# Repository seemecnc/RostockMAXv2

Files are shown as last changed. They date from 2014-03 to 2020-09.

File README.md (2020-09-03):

# Rostock MAX v2 3D Printer by SeeMeCNC #

### A hybrid design between the Rostock MAX build volume and Orion delta shape and overall design. ###

### Larger build volume than Orion Delta (similar to Rostock MAX) but much faster assembly and stiffer frame###

#### Build volume is appx. 11" diameter by 14+" tall. ####

# Visit seemecnc.com for documentation under the menu tab SUPPORT > ARCHIVE

Specs:

Overall machine size - 20" diameter by 40" tall (including spool mounted on top)

Power Supply - 450w ATX PSU (12v 20+amps)

Heated Bed - Onyx (same as Rostock MAX)

Electronics - RAMBo by UltiMachine

Filament - 1.75mm ABS/PLA/HIPS/Taulman Nylon/T-Glase/other 
Anything withe less than 240c printing temps

HotEnd - SeeMeCNC 1.75mm bowden 

Extruder - EZStruder set up as bowden drive

Human/Machine interface - LCD control with onboard SD card

Frame material - HP Melamine laminate

These files are distributed openly without warranty, as is/where is under the GPL liscense from previous inspirational designs such as the Rostock by Johann. The EZ Struder was inspired by whosawhatsis as well as sgraber's i3 extruders.

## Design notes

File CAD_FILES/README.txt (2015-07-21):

For Injection Molded/CNC Machined part source files, see the RostockMAX github repo.
The parts are same for V1 / v2

7/21 J.O.
REV5 dxf files eliminated the lasercut truck plates for cheapskates since moving to I.M. style and opened up some clearance holes for thumb screws to mount the side covers and LCD panel

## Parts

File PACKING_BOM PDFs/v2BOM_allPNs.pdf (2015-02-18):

# Packing List

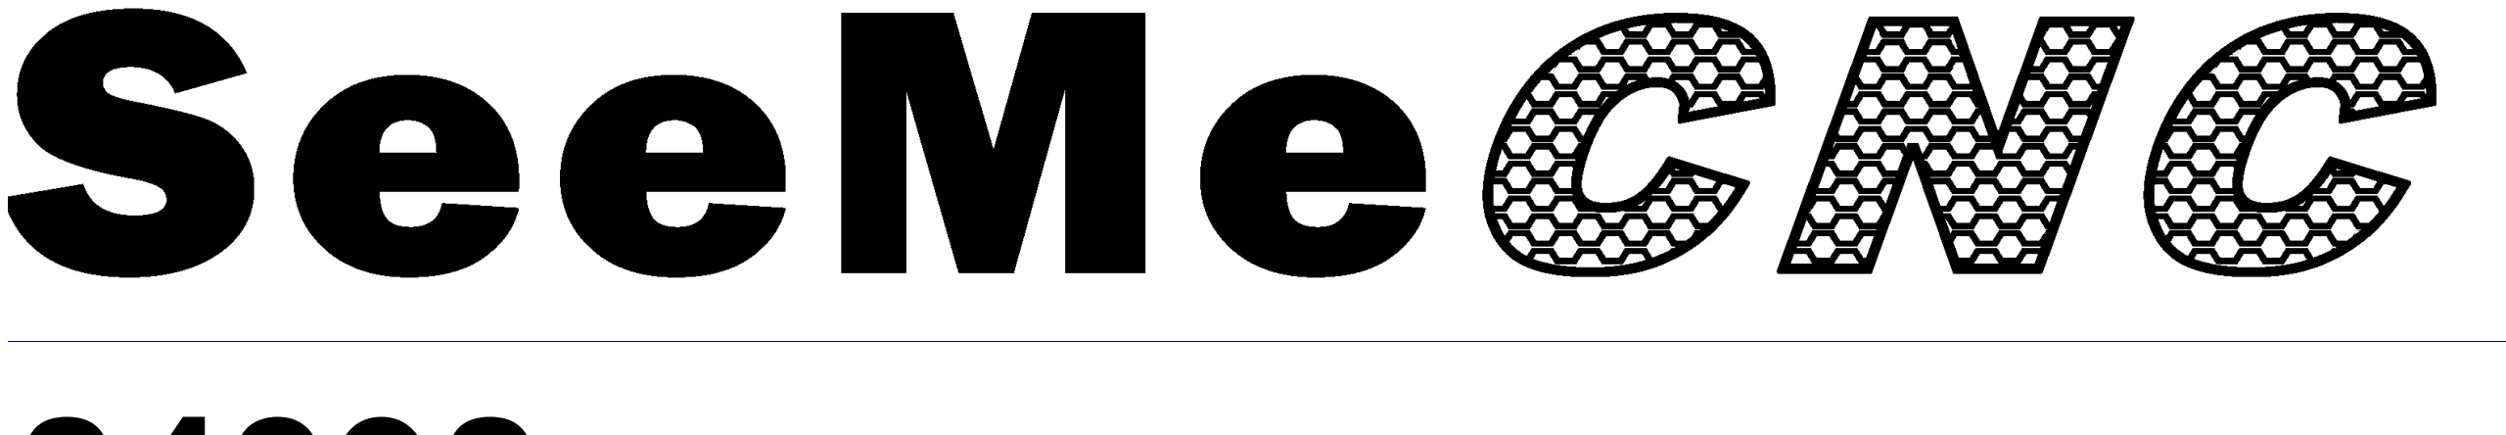
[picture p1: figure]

# 84398 Rostock MAX V2 3D Printer Kit BLACK

item # | qty | Description | Where is this item used?
84301 | 1 | Laser Cut Sheets (3 full 1 partial)
84302 | 1 | Smoke Acrylic Parts Pack
84392 | 1 | Rostock MAX V2 Electronics Parts and Hardware Pack 4 (inside box)
26702 | 1 | ATX Power Supply 450W
26602 | 1 | Borosilicate Glass Build Plate 300mm Dia. X 3mm Thick ( inside box)
84395 | 1 | Rostock MAX V2 Hardware Pack 3 (inside box)
84391 | 1 | Rostock MAX V2 Hardware Pack 1 (inside box)
84393 | 1 | Rostock MAX V2 Hardware Pack 2 (inside box)
68310 | 3 | T Slot Rail 1" (25mm) Square x 32" (812mm) Long Aluminum
©2014 SeeMeCNC | 18-Feb-15 | 84398 | Rostock MAX V2 3D Printer Kit BLACK | Page 1 of 1

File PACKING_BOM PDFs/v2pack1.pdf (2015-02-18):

# Packing List

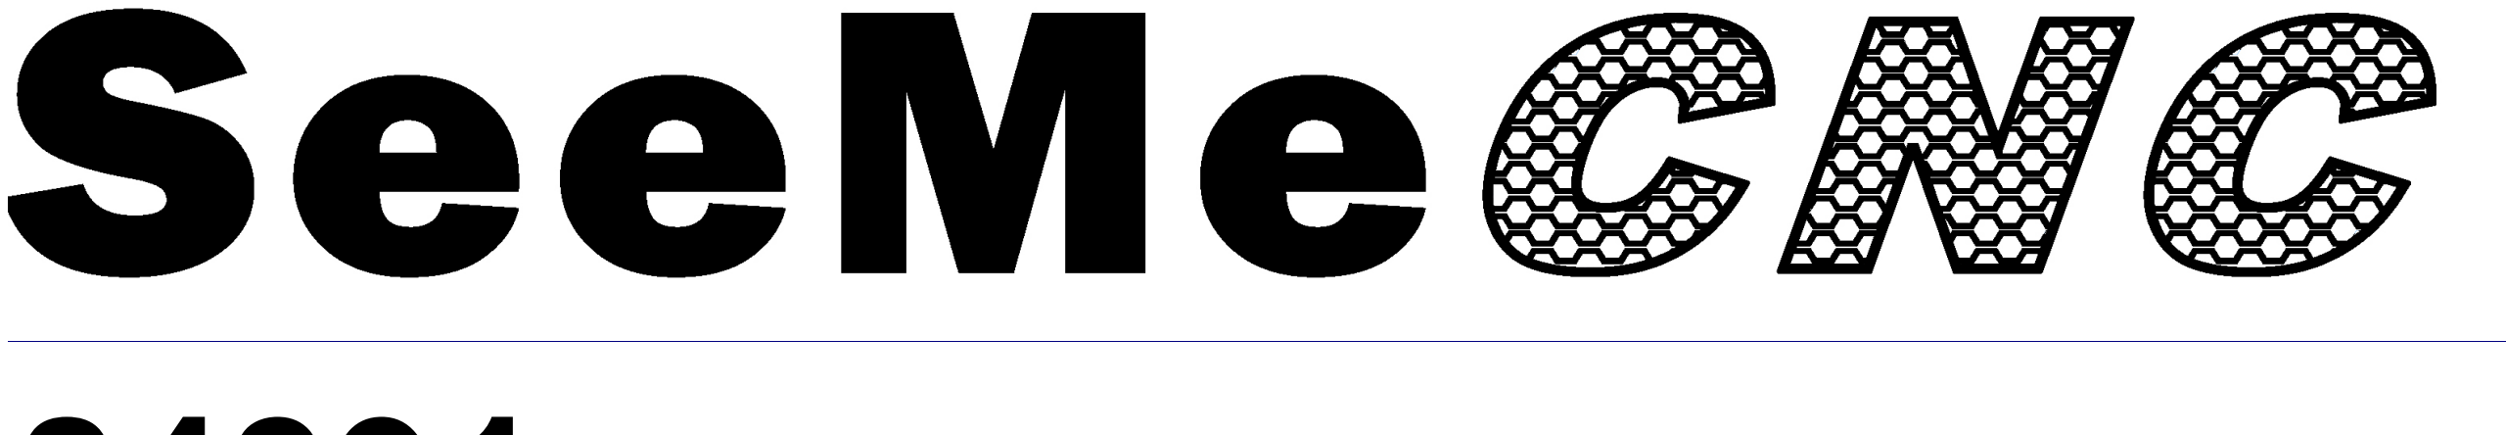
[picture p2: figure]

# 84391 Rostock MAX V2 Hardware Pack 1

item # | qty | Description | Where is this item used?
44010 | 6 | Rubber Foot | | On the bottom of the baseplate.
17505 | 6 | Leg for 44010 Foot | | On the bottom of the baseplate.
30450 | 18 | #6 SAE Flat Washer Stainless Steel | ONLY used on the 608 idlers that go in the top/bottom of the tslot rails.
30449 | 6 | #4 SAE Flat Washer Stainless Steel | Belt clamp screws.
35065 | 21 | 608 Ball Bearing | | Cheapskates and belt idlers.
30650 | 14 | 2-56 x 5/8"L Pan Head Phillips Machine Screw ( zinc plate ) | 4 for the LCD faceplate and 6 for mounting endstops.
30222 | 10 | 4-40 Blind T-Nut (zinc plate) | belt clamping and RAMBo mounting
29999 | 1 | SHCS 10-32 x 5/8 L 18-8 SS | To tap holes for 10-32 nylon thumb screws.
29998 | 6 | 10-32 x 5/8" Pan Head Screw Nylon | On the bottom of the baseplate.
30170 | 6 | 10-32 Nylon Finish Nut | On the bottom of the baseplate.
30172 | 9 | 10-32 x 3/4" Knurled Thumb Screw Black Nylon | Right/left base covers and holds LCD panel on.
30121 | 4 | 6-32 x 1/2" Slotted Pan Head Screw Nylon | PSU mounting.
30033 | 31 | 6-32 x 1" L Phillip Pan Head Screw Stainless | Misc. general assembly of base/table and extruder mount/spoolholder.
30006 | 6 | SHCS 6-32 x 5/8" | 18-8 SS | For mounting the U Joint mounts to the cheapskate plates.
30034 | 12 | 6-32 x 1.75" L Phillip Pan Head Screw Stainless | 608 idlers in motor mounts and tops and also 3 for the hotend standoffs
30164 | 63 | 6-32 Nylon Lock Nut Stainless Steel | All 6-32 hardware gets these lock nuts.
30037 | 14 | 6-32 x 2.0" L Phillip Pan Head Screw 18-8 SS | Cheapskate plates that hold bearings and 2 for the EZStruder mounting.
30135 | 15 | 6-32 x 1/2" 18-8 SS Phillips Flat Head | Inside of base and top side plates, to retain acrylic panels, and 3 endstop trig
30419 | 25 | 1/4-20 x 1/2" Button Head Cap Screw Stainless | T slot mounting.
32005 | 25 | T SLOT Nut for 1" size 1/4-20 | T slot mounting
30236 | 4 | 4-40 x 3/4"L Phillip Flat Head Machine Screw Stainless | For mounting RAMBo to electroncis mount.
30232 | 6 | 4-40 x 1/2" L SHCS Stainless | Belt clamps.
30642 | 14 | 2-56 Finish Nuts ( zine plate ) | 4 for the LCD faceplate and 6 for mounting endstops.
30250 | 14 | #4 Pan Head Phillips x 3/8" Sheet Metal Type B - Stainless Steel | 2 for LCD sides, rest for t slot stop screws inside motor mount plates to keep
30318 | 12 | M3 - .50 x1 0mm Phillip Pan Head Machine Screw 18-8 SS | Stepper motor mounting.
©2014 SeeMeCNC | 18-Feb-15 | 84391 | Rostock MAX V2 Hardware Pack 1 | Page 1 of 1

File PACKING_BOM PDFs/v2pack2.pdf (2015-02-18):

# Packing List

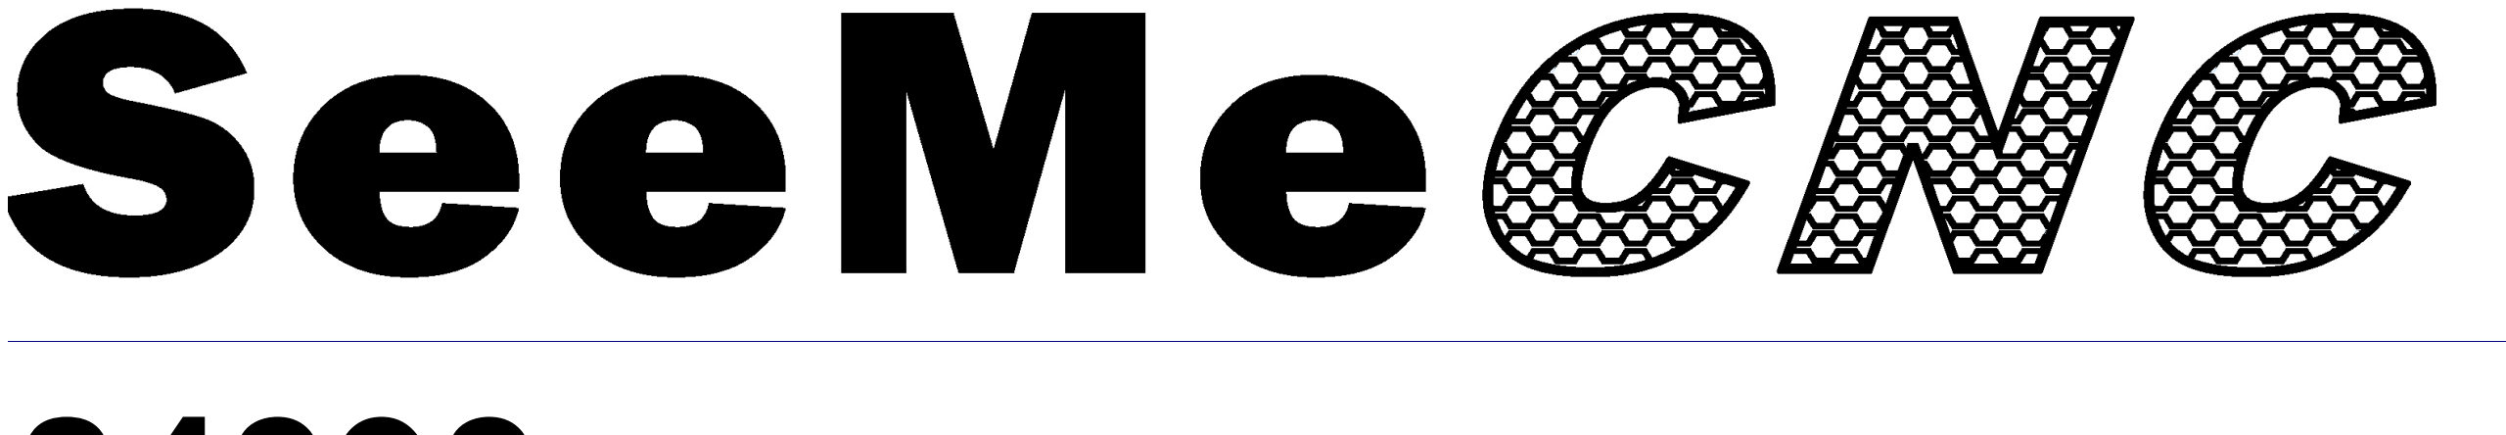
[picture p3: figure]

# 84393 Rostock MAX V2 Hardware Pack 2

item # | qty | Description | Where is this item used?
68326 | 12 | 608 Cheapskate Carriage Bearing Spacer | Fixed black spacers for cheapskates.
68340 | 18 | 608 Cheapskate Idler Bearing Spacer | Large black round spacers for belt idlers.
68315 | 12 | 608 Cheapskate Eccentric Carriage Tensioner Spacer | Eccentric grey cammed parts for adjusting tension.
68334 | 3 | Hot End Platform Spacer (machined Aluminum) | 1" long.
68325 | 6 | Universal Joint Axle 3-1/8" Long
68309 | 12 | Universal Joint (Machined Aluminum)
©2014 SeeMeCNC | 18-Feb-15 | 84393 | Rostock MAX V2 Hardware Pack 2 | Page 1 of 1

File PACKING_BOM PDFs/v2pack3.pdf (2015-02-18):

# Packing List

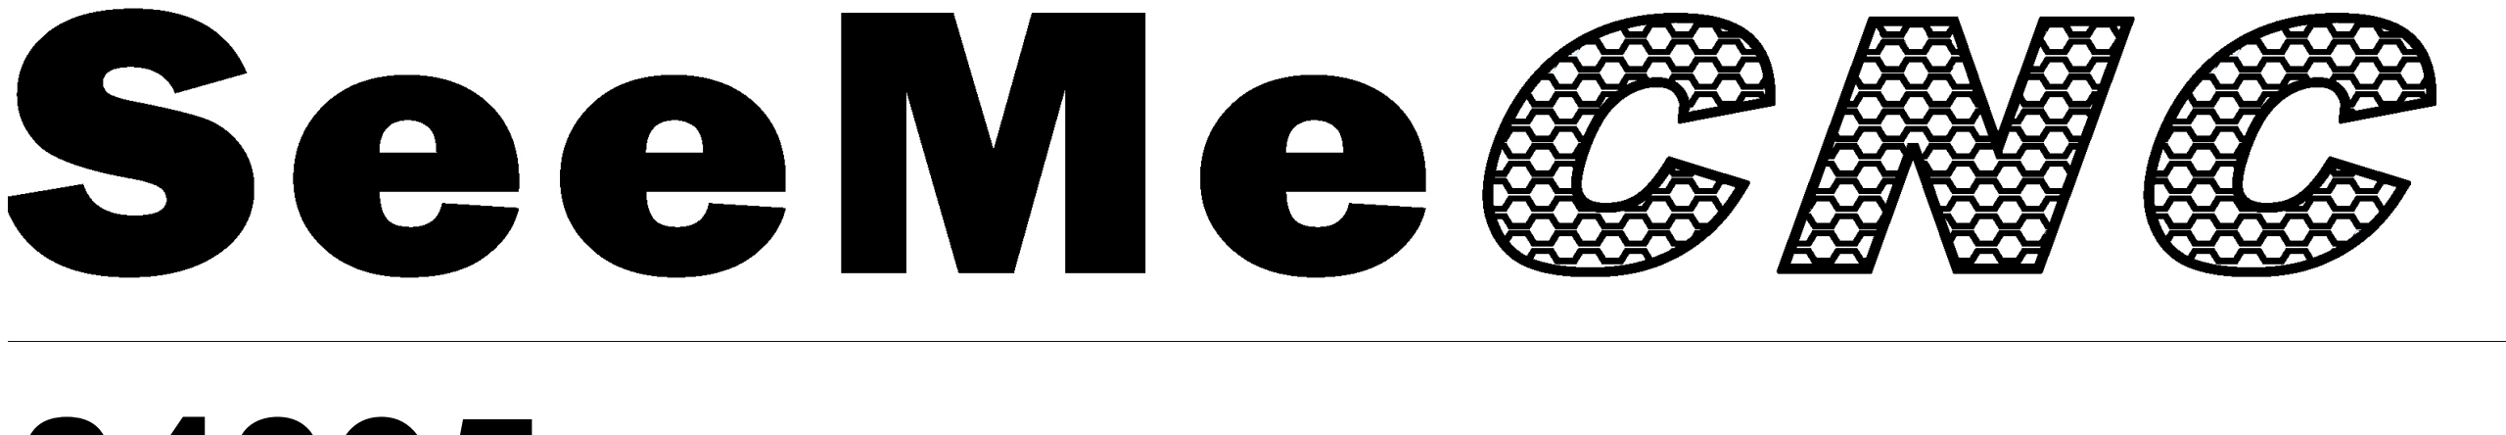
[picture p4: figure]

# 84395 Rostock MAX V2 Hardware Pack 3

item # | qty | Description | Where is this item used?
71505 | 20 | Plastic Bearing Roller 1/8"ID x 3/8"OD x 0.156"W | 4 for RAMBo mount and 6 for belt clamps.
26164 | 12 | Wire Tie (small) | To make neater wiring, esp. for strain relief on hotend platform and to attach
39835 | 1 | 20T Timing Pulley GT2 2mm Pitch (Pack of 3 w/6 setscrews and allen key)
68332 | 3 | Carriage Base for Universal Joint (injection molded) | Outer 'tabs' have been removed to allow spring clips to be used.
70832 | 1 | Platform (Spring Clip Style)
87940 | 6 | Spring Clip for U Joint
71566 | 1 | Gear (15 Tooth) | To press on stepper shaft for hand turning the extruder.
58761 | 6 | Binder Clip | For clamping glass build plate.
©2014 SeeMeCNC | 18-Feb-15 | 84395 | Rostock MAX V2 Hardware Pack 3 | Page 1 of 1

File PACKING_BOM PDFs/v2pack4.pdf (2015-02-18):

# Packing List

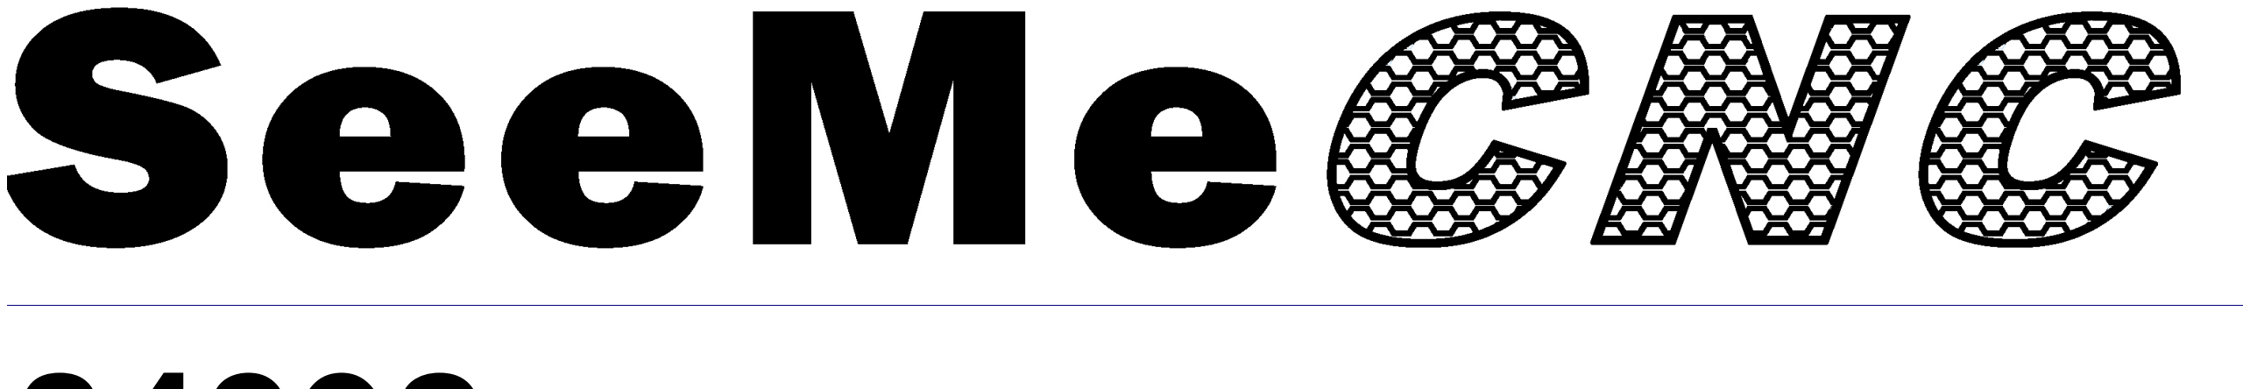
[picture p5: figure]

# 84392 Rostock MAX V2 Electronics and Hardware Pack 4

item # | qty | Description | Where is this item used?
26710 | 1 | RAMBo Electronic Control Board
26708 | 1 | USB Cable
58770 | 1 | Onyx Heated Bed Kit | Includes 6 4-40 x 3/4" flat heads, 6 4-40 t nuts, 6 plastic bearing roller, thermi
26720 | 1 | LCD Smart Controller With SD Card
26711 | 1 | LCD to RAMBo Adapter Kit
26169 | 1 | Knob Soft Touch 5mm ID | For LCD.
26501 | 4 | Nema 17 Stepper Motor 4800gcm holding torque | For three towers and extruder motor.
26175 | 1 | Rocker Switch, Black Round | Power switch.
26174 | 2 | Spade Terminal Crimp for Switch | For use on new power switch to make it removeable.
26309 | 1 | Fan 25mm X 25mm X 10mm | PEEK blower fan.
26173 | 1 | FAN 40mm x 40mm x 10mm | RAMBo cooling fan, goes on back of RAMBo electroncis mount blowing ON t
26722 | 10 | 22/4 Wire (by the foot) | For extending stepper motor for extruder.
26728 | 15 | 26AWG 7 Strand Wire BLACK Thin Wall PVC (by the foot) | For hotend PEEK fan and PART fan.
26726 | 15 | 26AWG 7 Strand Wire RED Thin Wall PVC (by the foot) | For hotend PEEK fan and PART fan.
26727 | 4 | 3/8" Dia. Expandable Black Mesh Loom (by the foot) | For wiring going from top plate down to platform.
26729 | 3 | 5/16" Heat Shrink Tubing (by the inch) | For cleaning up the ends of the mesh loom.
39910 | 1 | Timing Belt GT2 series 2mm pitch Neoprene (3 pieces 76" long)
68336 | 24 | Bearing Sleeve | For cheapskates.
68303 | 6 | ARM for Rostock MAX
70780 | 1 | EZStruder Cold End Kit | Includes stepper motor mounting hardware.
68394 | 1 | 1.75mm Bowden Hot End Assembly | Includes all hotned parts to assemble hotend, and 24" bowden tube w/ 2 ptc fi
26171 | 1 | Blower 30mm X 30mm X 10mm 12V DC | 0
26172 | 2 | Butt Splice Connector 16-14AWG | Hot End
26721 | 10 | 18/4 Wire (by the foot) | Hot End / Thermistor Wiring
©2014 SeeMeCNC | 18-Feb-15 | 84392 | Rostock MAX V2 Electronics and Hardware Pack 4 | Page 1 of 1

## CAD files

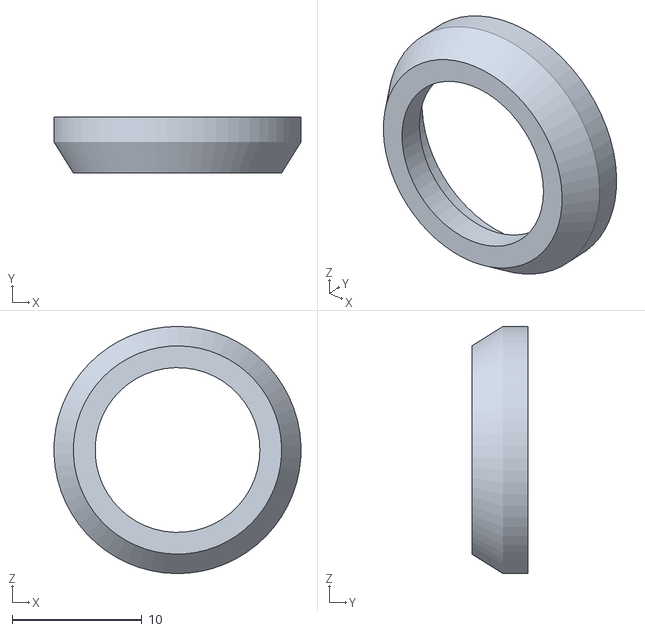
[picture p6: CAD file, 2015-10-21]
CAD_FILES/STL/843XX Rostock Max v2 Assembly - 70850 IM Ball Joint Carriage Assembly AXLE-4 87941 Bearing Sleeve-1.STL
19.0 x 4.35 x 19.0

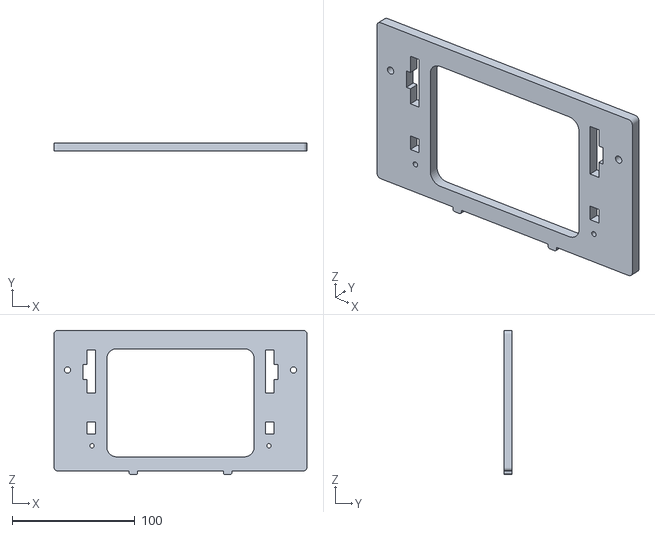
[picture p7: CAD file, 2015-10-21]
CAD_FILES/STL/843XX Rostock Max v2 Assembly - 87912 LCD Frame-1.STL
206.0 x 6.90 x 117.5

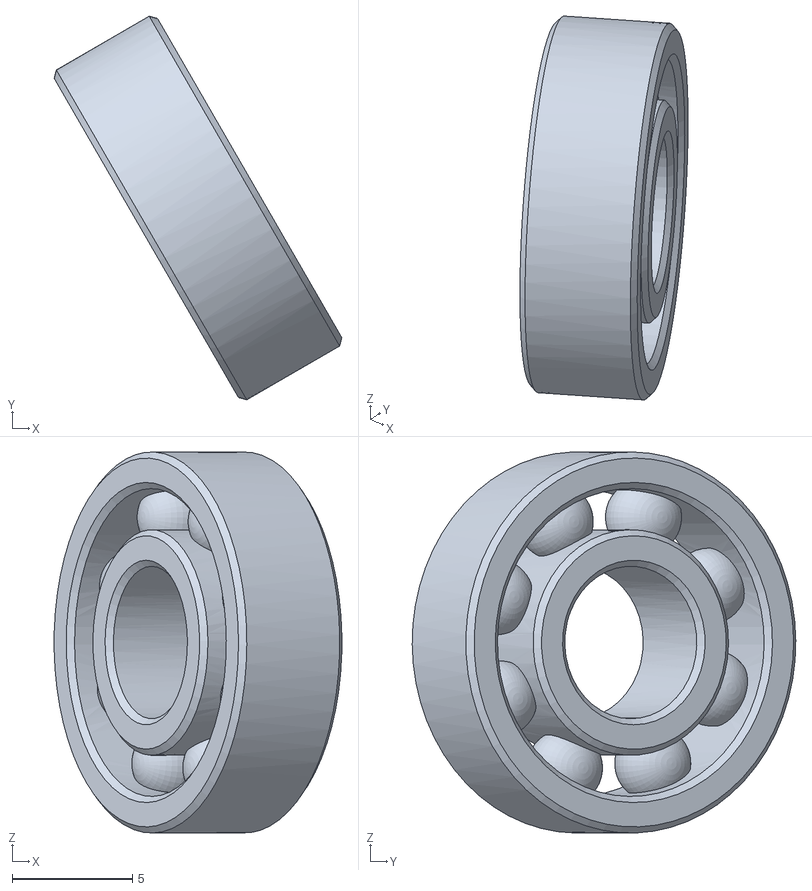
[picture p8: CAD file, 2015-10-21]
CAD_FILES/STL/843XX Rostock Max v2 Assembly - 70850 IM Ball Joint Carriage Assembly AXLE-5 0250ID - 0625OD - 0196W-1.STL
12.0 x 16.0 x 15.9

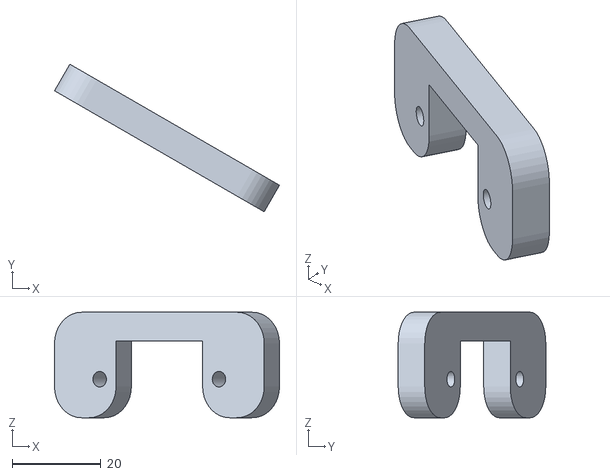
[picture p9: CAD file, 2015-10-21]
CAD_FILES/STL/843XX Rostock Max v2 Assembly - 70769 Spacer-3.STL
50.6 x 33.2 x 23.8

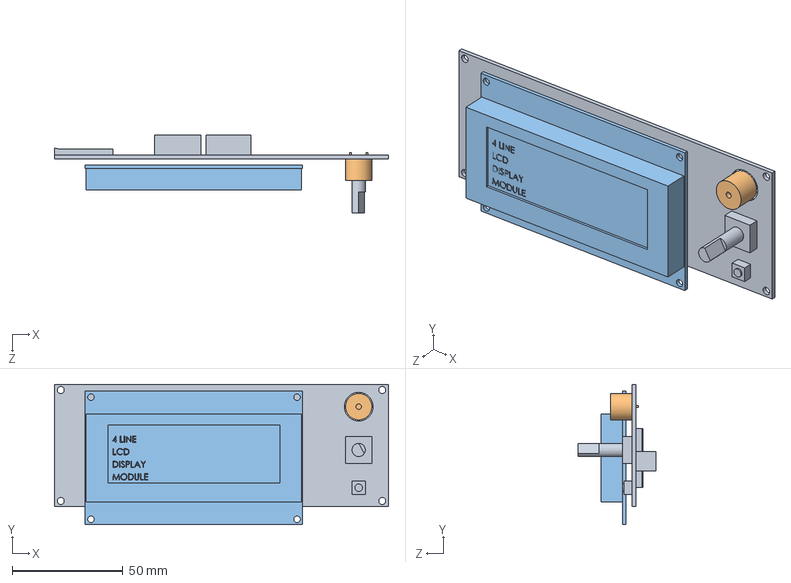
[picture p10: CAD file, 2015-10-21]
CAD_FILES/Solidworks/Smart Controller reprapdiscount.SLDASM
150.5 x 63.2 x 35.0 mm
MAIN_BOARD_reprapdiscount_smart_controller
Piezo Beeper HSD
LCD 4 Line reprapdiscount style

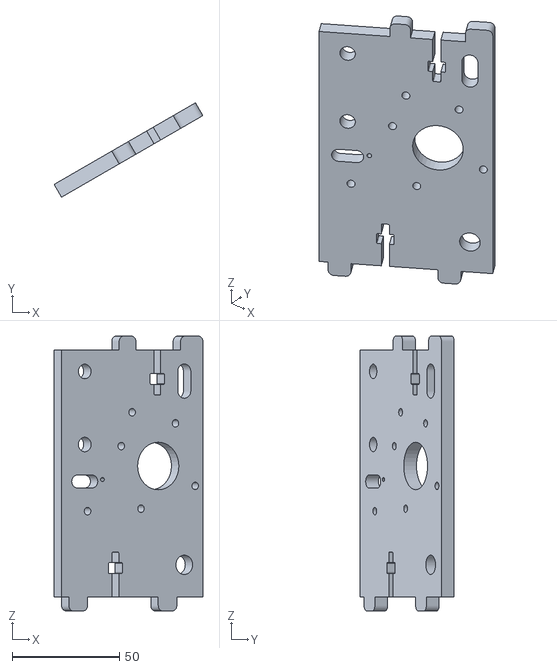
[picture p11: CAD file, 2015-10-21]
CAD_FILES/STL/843XX Rostock Max v2 Assembly - XZ Stepper Motor Assembly-1 84307Motor Mount-1.STL
69.3 x 44.0 x 128.0

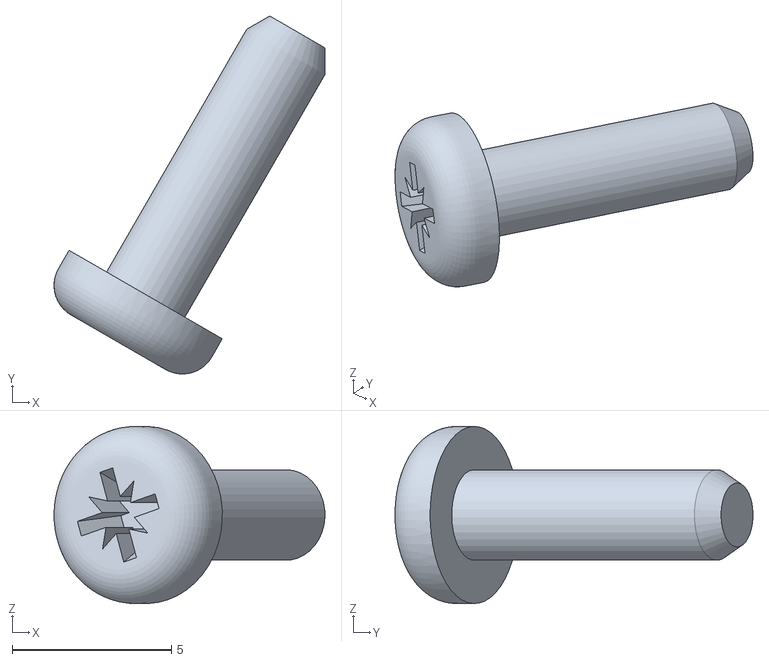
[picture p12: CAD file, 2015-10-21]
CAD_FILES/STL/843XX Rostock Max v2 Assembly - 70780 EZStruder-1 No 4 x 0375L PANHTS SS Sheet Metal PANHTS 0.112-24-type II-B-0.375-N-5.STL
8.51 x 11.2 x 5.56

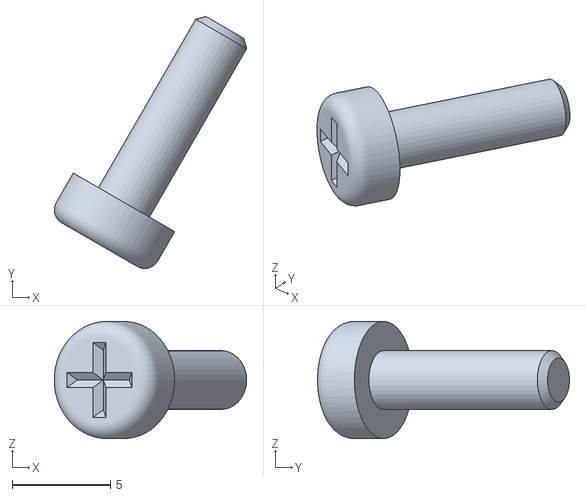
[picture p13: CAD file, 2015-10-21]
CAD_FILES/STL/843XX Rostock Max v2 Assembly - Y Stepper Motor Assembly-1 M3-0.5 x 10mm L Phillip Pan Head Stainless-4.STL
9.80 x 12.8 x 5.97

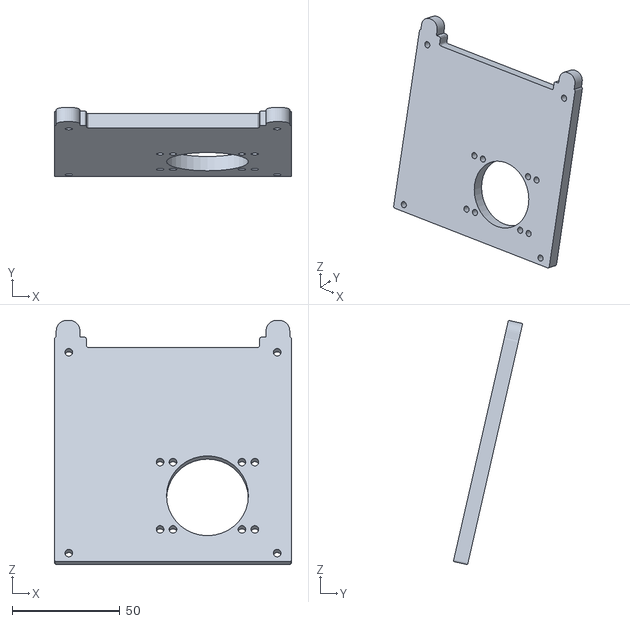
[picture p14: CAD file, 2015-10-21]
CAD_FILES/STL/843XX Rostock Max v2 Assembly - 84328 Rambo Mounting Plate-1.STL
110.0 x 32.2 x 113.5

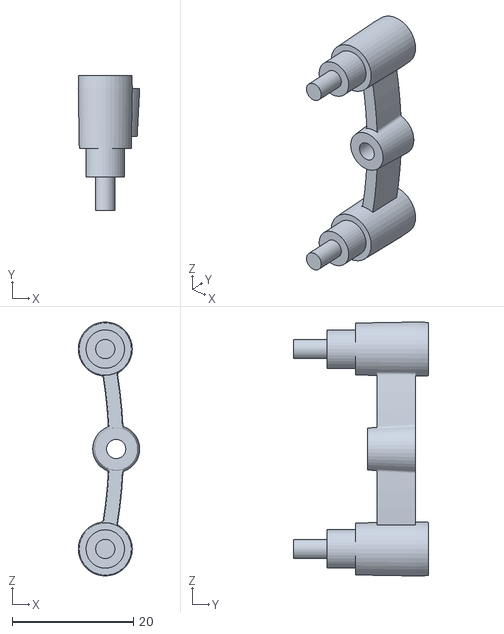
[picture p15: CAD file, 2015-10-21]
CAD_FILES/STL/843XX Rostock Max v2 Assembly - 70850 IM Ball Joint Carriage Assembly AXLE-4 70853 Outer Carriage Spring Arm-1.STL
10.2 x 22.2 x 41.9

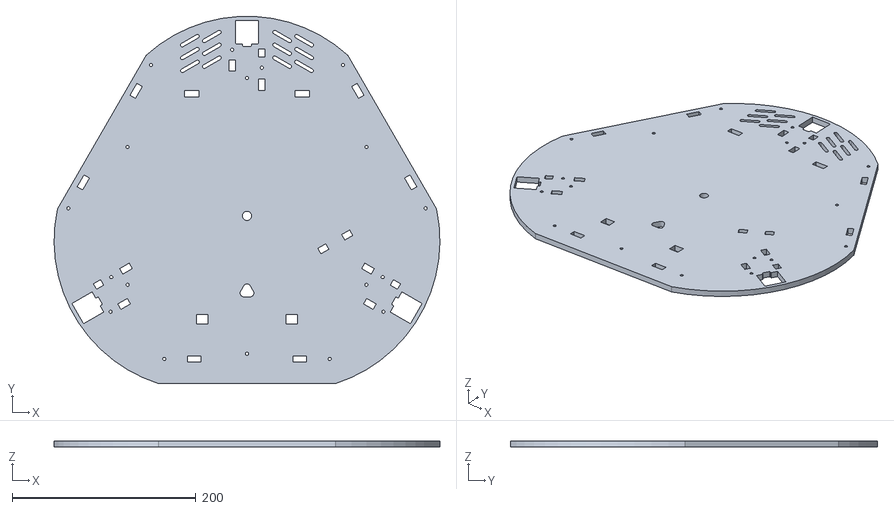
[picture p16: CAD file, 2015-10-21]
CAD_FILES/STL/843XX Rostock Max v2 Assembly - 84303 Base Top-Plate-1.STL
419.9 x 399.3 x 6.80

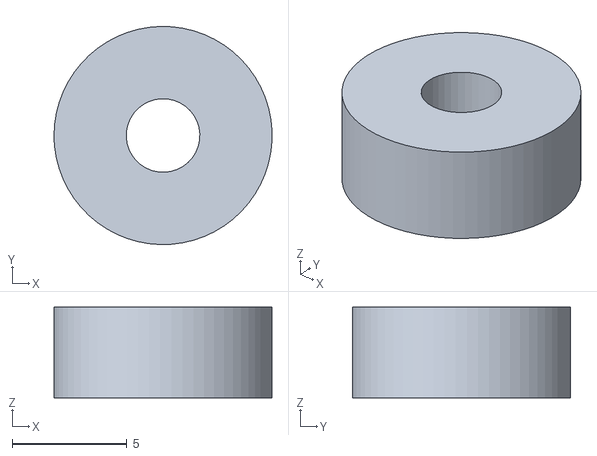
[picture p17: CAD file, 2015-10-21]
CAD_FILES/STL/843XX Rostock Max v2 Assembly - 71505 Plastic Bearing 0125ID x 0375OD x 0156W-7.STL
9.52 x 9.52 x 3.97

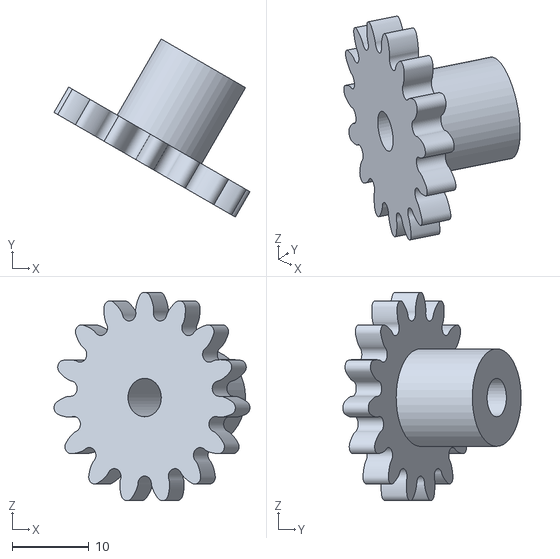
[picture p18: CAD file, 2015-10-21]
CAD_FILES/STL/843XX Rostock Max v2 Assembly - 70780 EZStruder-1 71566 Gear 15T 0950PD-1.STL
25.5 x 23.2 x 27.1

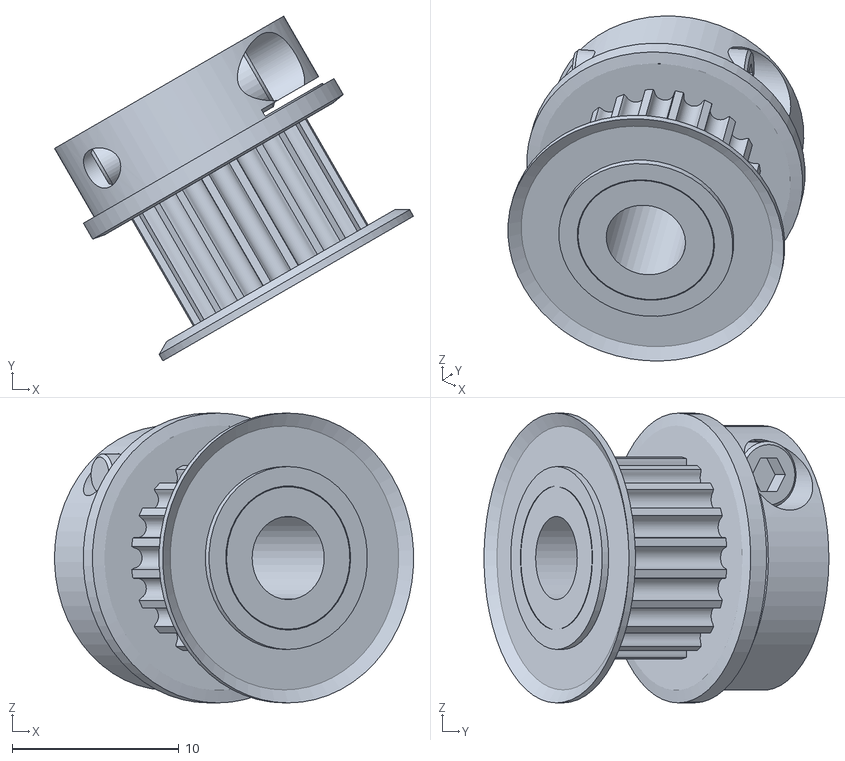
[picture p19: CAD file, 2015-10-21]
CAD_FILES/STL/843XX Rostock Max v2 Assembly - XZ Stepper Motor Assembly-1 39835 Timing Pulley 20T GT2-2-1.STL
21.6 x 20.7 x 17.4

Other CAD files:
CAD_FILES/IGES/843XX Rostock Max v2 Assembly.IGS
CAD_FILES/STL/843XX Rostock Max v2 Assembly - 84305 Side-3.STL
CAD_FILES/STL/843XX Rostock Max v2 Assembly - XZ Stepper Motor Assembly-2 39835 Timing Pulley 20T GT2-2-1.STL
CAD_FILES/STL/843XX Rostock Max v2 Assembly - 70850 IM Ball Joint Carriage Assembly AXLE-7 No 4 x 0250L PANHTS SS Sheet Metal PANHTS 0.112-24-type II-B-0.25-N - Copy-3.STL
CAD_FILES/IGES/0250ID - 0625OD - 0196W.IGS
CAD_FILES/IGES/17505 LEG.IGS
CAD_FILES/IGES/39835 Timing Pulley 20T GT2-2.IGS
CAD_FILES/IGES/4-40 X 0500 PHILLIP FLAT HEAD.IGS
CAD_FILES/IGES/44010 FOOT.IGS
CAD_FILES/IGES/58763 Bed Insulator for Onyx R5.IGS
CAD_FILES/IGES/6-32 X 0500 Phillip Flat Head Screw Stainless.IGS
CAD_FILES/IGES/6-32 X 1 PHILLIP FLAT HEAD.IGS
CAD_FILES/IGES/608-bearing.IGS
CAD_FILES/IGES/68325 U Shaft Axle.IGS
CAD_FILES/IGES/68340 Bushing Washer 3mm.IGS
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

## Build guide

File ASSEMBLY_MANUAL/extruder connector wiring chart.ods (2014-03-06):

Pin | Color
1 | Green
2 | Red
3 | Black
4 | White

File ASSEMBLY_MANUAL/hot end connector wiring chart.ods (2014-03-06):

Pin | Color
1 | Red
2 | Black
3 | Green
4 | White

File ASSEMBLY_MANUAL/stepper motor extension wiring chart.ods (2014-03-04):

Pin | Stepper Color | Extension Color
1 | Green | Green
2 | Red | Red
3 | Blue | Black
4 | Yellow | White

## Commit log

2014-02-04 Initial Upload
    Uploading merged CAD files from MCX of Rostock/Orion and laying out R3
    files
2014-02-04 Updated mcx file
    updated colors for laser
2014-02-04 more cad updates
2014-02-04 added logo
    added logo, fixed hole orientation
2014-02-05 cad updates
    updating top plate mounting
2014-02-06 Laying out Top cover plate
    Layed out cover for top and acrylic parts
2014-02-06 added new top plate and onyx ins
    added insulator and relyaed some parts
2014-02-06 more cad updates
    more updates
2014-02-06 added DXF of MCX file
    Added DXF file THIS MAY NOT BE CURRENT FILES DUE TO NOT EXPORTING THE
    DXF FROM MCX ! ! !
    [LC_270-SHEETS.DXF]
2014-02-06 updated cad
2014-02-06 cad fixes
    need to move side plates on right/left back some more
2014-02-07 updated cad files
    added second extruder mounting to top plate for those daredevils
2014-02-07 updated DXF file
    updated DXF file for lasercutting
    [LC_270-SHEETS.DXF]
2014-02-07 cad updates
    cad updates, moved rambo back, enlarged cooling holes and misc....
2014-02-07 angled extruder mount and updated DXF
    angled extruder mount to help position bowden tube and updated DXF file
    [LC_270-SHEETS.DXF]
2014-02-10 added logos and updated DXF
    added logos and Updated DXF
    [LC_270-SHEETS.DXF]
2014-02-14 updated MCAM file
    added missing wire tie holes
2014-02-14 Updated DXF files
    Updated DXF's
    [LC_270-SHEETS.DXF]
2014-02-18 updated CADS
    updated cad and dxf files, flipped acrylic lcd faceplate to cut top
    down, adding logo
    [LC_270-SHEETS.DXF]
2014-02-24 updated CAD files
    Added more clearance for t nuts on power supply mount and re-nested all
    parts/sheets
    [SHEET1.DXF, SHEET3.DXF]
2014-02-24 removed junk files
    removed junks
    [SHEET1.DXF, SHEET3.DXF]
2014-02-24 updated DXF files
    [LC_270-SHEETS.DXF]
2014-02-25 Updated CAD files
    Updated both mcx and dxf files
    [LC_270-SHEETS.DXF]
2014-03-03 Editing continues....
    [No. 4 x 3125 pan head sheet metal.SLDPRT, top plate base.SLDPRT, top plate base.dxf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]
2014-03-04 Editing continues
    [stepper motor extension wiring chart.ods]
2014-03-05 Editing continues.
    [hot end connector wiring chart.ods]
2014-03-05 updated cad file
2014-03-06 Editing continues!
    [extruder connector wiring chart.ods, hot end connector wiring chart.ods, hot end mounting plate spacer.SLDPRT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]
2014-03-07 updated CAD files
    Moving to DXF files only on git, confusing with MCX and DXF's
    [ACRYLIC_ALL_PARTS.DXF, LC_270-SHEETS.DXF]
2014-03-08 Instructions for assembly are now complete.
2014-03-10 Reached 1.0! Assembly & Calibration sections are fully completed, BOM is correct. Next step will cover printing the fan shrouds as the first prints.
2014-03-12 Change advice on issues with axles.
2014-03-19 Many little edits, clarifications and fixes.
    [upper tower mount v2.SLDPRT, upper tower mount v2.dxf]
2014-03-23 new illustrations, clarification edits.
    [vertical support.SLDPRT, vertical support.dxf]
2014-06-25 Added hot end power LED connection info.
2014-06-30 Updated DXF file
    Added tower labeling
    [LC_270-SHEETS.DXF]
2014-07-16 Updated ALL Cad files
    Updated cad files to show revisions and also left a readme about cad
    source for non lasercut files are in the RostockMAX git repo
    [843XX ROSTOCK MAX V2 REV2.DXF, LC_270-SHEETS.DXF, OLD ---- SHEET3 REV2.DXF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]
2014-07-23 Added new revision heated bed insulator
    Added insulator dxf file for newer (rev5 and up) heated beds
    [58763 BED INSULATOR FOR ONYX R5.DXF]
2014-07-27 Added info on new Rev6 Onyx and new part updates.
    [Onyx R6 Support Plate.SLDPRT]
2014-07-30 Updated to REV4 Cad files
    Added more cooling inlet/outlets in base box for cooling issues with
    bigger power supplies
    [SHEET1.DXF, SHEET2.DXF, SHEET3.DXF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]
2014-08-08 Kysan motor update. Started work on MatterControl edition.
2014-08-20 Added info on injection molded --joints
2014-08-27 Corrected length of hot end standoff.
2015-02-18 Added PACKING_BOM PDFs folder
    Added our internal packing/BOM's for v2 kits
2015-07-21 Updated some dxf files
    removed lasercut trucks from LC files since switching to Inj. Molded
    style and updated a few holes for clearance of thumb screws
2015-10-21 Added Solidworks, IGS, and STL Files
    Added modeling files in Solidworks, IGS, and STL formats.
    [0250ID - 0625OD - 0196W.IGS, 0250ID - 0625OD - 0196W.SLDPRT, 17505 LEG.IGS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]
2020-04-26 Create 70832 platform r2.STL
    added missing file
    [70832 platform r2.STL]
